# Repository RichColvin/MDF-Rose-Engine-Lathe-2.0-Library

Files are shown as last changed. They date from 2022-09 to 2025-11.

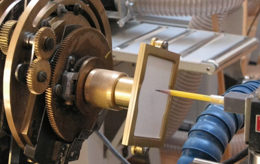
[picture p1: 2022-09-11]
NextionPreV22/Images/PaperChuck.png

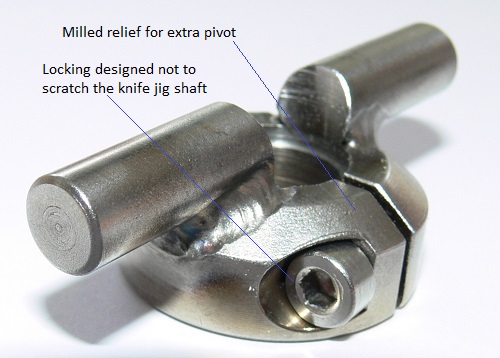
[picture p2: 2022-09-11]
Documents/MASTER - Documents/Images/Desktop/Tormek Add-on Parts/pivot_collar_3.JPG

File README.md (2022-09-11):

# MDF Rose Engine Lathe 2.0 Library
Code and images used for the MDF Rose Engine Lathe 2.0 Library web site (https://mdfre2.colvintools.com/)

This work is licensed under a Creative Commons Attribution-ShareAlike 4.0 International License.

To the extent that material may appear to be infringed, I assert that such alleged infringement is permissible under fair use principles in U.S. copyright laws. If you believe material has been used in an unauthorized manner, please contact me at the eMail listed above.

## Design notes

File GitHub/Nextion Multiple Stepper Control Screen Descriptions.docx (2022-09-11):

Nextion Multiple Stepper Control Screen Descriptions

V: 26r

Splash Screen

Purpose: Initialize program

Buttons explanation: Touching one of the top row buttons will take you to that screen. The ‘Load Ini’ button in the lower right corner will load motor settings from an ini file named 4Axes.ini. Restarting the program may be necessary for all the settings to be active.

4-Axes Driver Board

# Main Screen

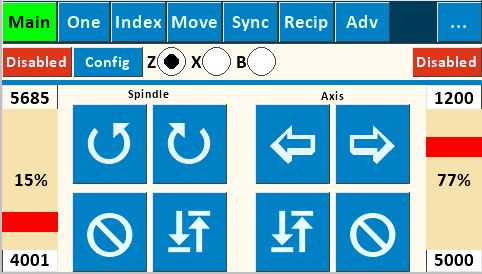
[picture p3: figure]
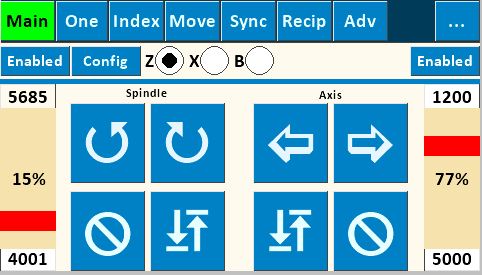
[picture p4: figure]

Purpose: Allows direct control of spindle speed and direction and auxiliary axis speed and direction independent of one another. Typically used for continuous spindle and/or continuous Axis motion (turning or facing cuts, continuous rose engine patterns on cylindrical or face surfaces., etc.).

Buttons explanation:

- “” (Counterclockwise) and “” (Clockwise) rotational arrows indicate direction of the Spindle. “”(In) and “”(Out) indicates direction of the selected axis. Rotation/movement continues until “” (Stop) is pushed.
- Right and left speed bars (for Spindle and Axes, respectively, are shown as a percentage of maximum speeds set on the Configuration Screen for “Main” and “Z, X, or B Axes”, respectively. Max speed and acceleration entry fields are shown at the top and bottom of each speed bar. These fields may also be set using the Configuration screen.
- “ “(Return): Returns the spindle or the selected axis to the start point of the previous operation.

# Number Pad Screen

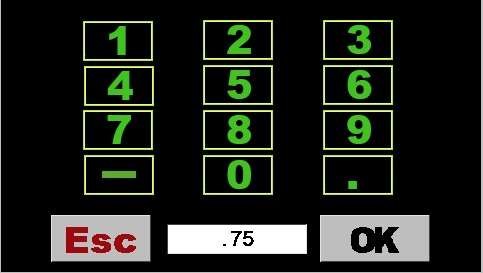
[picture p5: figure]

Purpose: This screen appears whenever any numerical value on any screen is tapped. Revise the number in the box by tapping the box multiple times to “backspace” over each digit or decimal point, and then re-enter the new value using the number pad buttons. Pressing “OK” saves the number back to the value box on the previous screen and returns user to that screen.

# Synchronization Screen

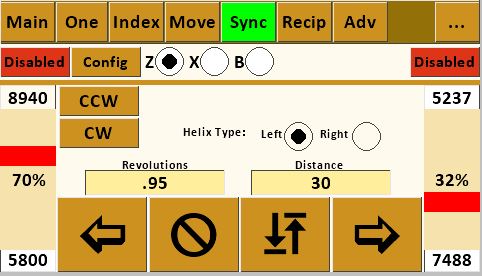
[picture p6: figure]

Purpose: Synchronizes the Spindle and Auxiliary Axis to produce helical patterns or threads on cylindrical surface of workpiece or to produce spirals on a face surface.

Buttons explanation:

- “Left” and “Right” determine whether helix runs clockwise or counterclockwise on the piece.
- “CW” (Clockwise) and “CCW” (Counterclockwise) index the spindle for the next cut path – either clockwise or counterclockwise per user design. Amount the spindle will index uses the value in “Size” set in the box on the Index #1 Screen (this value could be either in divisions of a circle or degrees depending upon which option is toggled on Index #1 Screen).
- “Revolutions” variable value determines how far around the piece the helix will travel based on the spindle rotating. The value of .5 illustrated will rotate spindle 360x.5=180 degrees.
- “Distance” variable value determines the cut length (amount of Z axis movement) and is dependent upon value entered in Setup Screen for “Distance/360”.
- Right and left speed bars (for Spindle and Axis, respectively, are shown as a percentage of maximum speeds set on the Configuration Screen for “Sync” and “Z Axis”, respectively. Note that slowest value on speed bars will “control” the other value.
- “”(In) and “”(Out) determine whether cut is made toward or away from headstock. Pattern will run the pre-determined “Distance” and then stop and wait for return direction instruction. User chooses whether to cut in both directions or retract cutter and return to start without cutting.
- “ “(Return): Returns both the spindle and the axis to the start point of the previous operation.
- See appendix for procedure for using the Synchronization Screen for thread cutting.

# Reciprocation – Axis Screen (Axial)

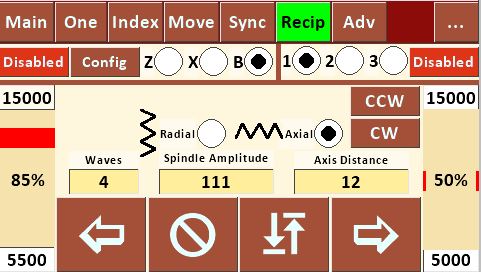
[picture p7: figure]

Purpose: Synchronizes Spindle and Auxiliary Axis to produce a reciprocating pattern along the longitudinal cylindrical surface of workpiece: It works by reversing spindle direction alternately while Z or X axis continues in the same direction.

Buttons explanation

- “1” Pattern is an equal angle on the up and down legs.
- “2” Pattern is a square wave.
- “3” Pattern is a like a sawtooth. The up leg is angled, the down leg is straight down.
- “CW” (Clockwise) and “CCW” (Counterclockwise) index the spindle for the next reciprocating cut path – either clockwise or counterclockwise per user design or desire. Amount the spindle will index uses the value set in the “Size” box on the Index #1 Screen (this value could be either in divisions of a circle or degrees depending upon which option is toggled on Index #1 Screen).
- “Wave Count” variable sets number of individual waves /\ to be cut along the cylinder.
- “Spindle Amplitude” variable sets “height” of each wave in degrees of rotation.
- “Axis Distance” variable determines the cut length for entire pattern (amount of Z, X, or B axis movement) and is dependent upon value entered in Setup Screen for “Distance/360”.
- “”(In) and “”(Out) determine whether cut is made toward or away from headstock. Note that “”(In) starts with a downward move and “”(Out) starts with an upward move (test your individual machine and apparatus to verify – your results may vary). Pattern will run the pre-determined “Axis Distance” and then stop and wait for return direction instruction. User chooses whether to cut in both directions or retract cutter and return to start without cutting.
- “ “(Return): Returns both the spindle and the axis to the start point of the previous operation.

# Reciprocation – Spindle Screen (Radial)

Purpose: Synchronizes Spindle and Auxiliary Axis to produce a sharp-pointed reciprocating pattern along the circumferential surface of a cylindrical workpiece: It works by alternately reversing Z or X axis direction while spindle continues rotating in the same direction.

Buttons explanation

- To navigate to this screen, start with “Rec” and toggle from Axial to Radial.
- “1” Pattern is an equal angle on the up and down legs.
- “2” Pattern is a square wave.
- “3” Pattern is a like a sawtooth. The up leg is angled, the down leg is straight down.
- Small “”(In) and “”(Out) move the Z or X axis to the next pattern starting position. Z or X axis movement will be the value of “Distance” set on the Move Screen for that axis.
- “Return” button rotates the spindle to the pattern start point.
- “Acceleration” and “Speed” values for this screen are set here for both Spindle, Z, and X axes. See notes on value limitations under Configuration Screen explanation. Because of synchronization of the spindle and Z or X axis speeds, one of the maximum speeds will control the other.
- “Wave Count” variable sets number of individual waves ( > ) to be cut along the cylinder.
- “Spindle Degrees” variable sets the circumferential distance around the cylinder for the total pattern. Entering 360 would wrap the pattern all the way around the cylinder; entering 90 would condense the whole pattern around just 90 degrees of the cylinder.
- “Axis Amplitude” variable sets “height” (distance along Z, X, or B axis) of each wave and is dependent upon value entered in Setup Screen for “Distance/360”.
- Large “”(In) and “”(Out) buttons determine the direction of cut around the spindle. Pattern will run the pre-determined “Spindle Degrees” then stop and wait for return direction instruction. User chooses whether to cut in both directions (either on the same cut path or on subsequent path) or retract cutter and return to the origin point without cutting.
- “ “(Return): Returns both the spindle and the axis to the start point of the previous operation.

# One Screen (Single Stepper Screen)

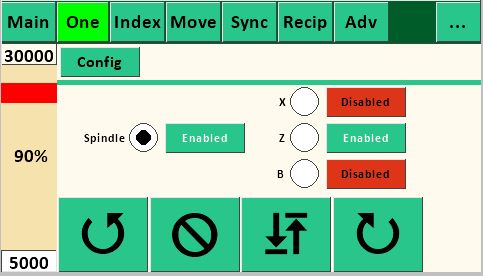
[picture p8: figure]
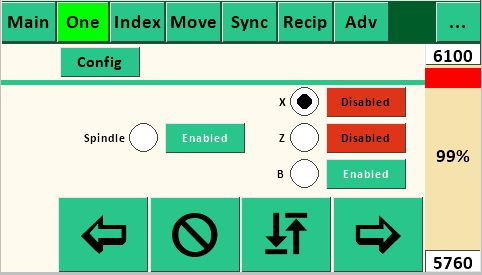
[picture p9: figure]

Purpose: Allows control of either the spindle or a single axis speed and direction. Useful for secondary spindle operation such as higher or lower speed functions than the Main Screen.

Buttons explanation

- “Enabled” shows status (either “Enabled” or “Disabled”) of either Spindle stepper motor or an Axis stepper motor as selected. If enabled, the motor is in locked status; if disabled, the selected motor can be repositioned. Default is “Disabled”. Primary use for these buttons is to lock the spindle or axis while performing another operation.
- “” (Counterclockwise) and “” (Clockwise) rotational arrows indicate direction of the Spindle .“”(In) and “”(Out) buttons indicate direction of an axis. Movement continues until “Stop” is pushed.
- Speed bar is shown only for the selected axis or spindle.

# Index Screen

Purpose: Allows indexing spindle for use in index work or other uses.

Buttons explanation

- 1-5: Individual indexes
- “Div” radio button sets the indexing to number of divisions of a full rotation, toggling to “Deg” sets the indexing to number of degrees.
- “Index” box shows current completed index
- “Next Index” shows ID of the next index. It will show lower ID if the CW button was last touched and higher if CCW button was touched
- Speed bar is shown as a percentage of maximum speeds set on the Configuration Screen for “Index”.
- “Divisions” of a circle or “Degrees”, depending upon which is toggled. Note that the value of the selected index (1 through 5) is used by the “CW” and “CCW” indexing movements on the Synchronization Screen and the Reciprocation – Axis Screen in either “Divisions” or “Degrees”, depending upon which is toggled.

# Index #2 Screen with file dropdown open

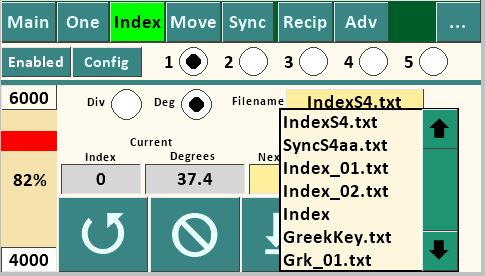
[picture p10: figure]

Purpose: Allows variable index sizes to be retrieved sequentially from a file stored on a microSD card. This feature could be used to place evenly spaced features (such as barleycorns) around the circumference of an ellipse (i.e. equal division of the ellipse), with the angular movement in degrees precalculated using a CAD program.

Selecting the filename text box will open a dropdown list of files located on the microSD card. Use the Up and Down arrows to traverse the file list. While the dropdown list is active, all other controls on the page are disabled. The dropdown list can be closed either by selecting a file, or by touching the Filename textbox. Each Index may have its own file.

The file format is ASCII text (numbers, letters, and decimal only) with each number on a new line, saved to the microSD card using a separate computer. Because the SD Card library only supports the 8.3 or Short File

Name convention, the file name must be a maximum 8 characters + a period + three-character extension (thus the 8.3); the name is not case sensitive. It's not necessary to have the extension, but the limit for the name is 8 characters when no extension is used. Multiple files can be loaded onto the microSD card for use on one or more work pieces as desired.

The counterclockwise and clockwise arrows determine direction of spindle movement during indexing. When using the “File” version, each successive index will read successive file numbers off the microSD card (in either “Div” or “Deg” as selected on this screen). When the end of the file is reached, “Size” will be reset to 0. The “Index” value will be increased when indexing clockwise and decreased when indexing counterclockwise. The read position of the file can also be set by editing the “Index” value.

The “Div” and “Deg” radio buttons and the “Enabled” button work the same as on the other Index screens above.

# Move Screen

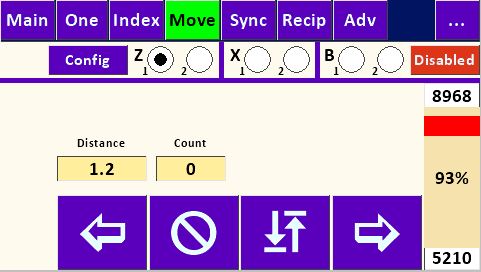
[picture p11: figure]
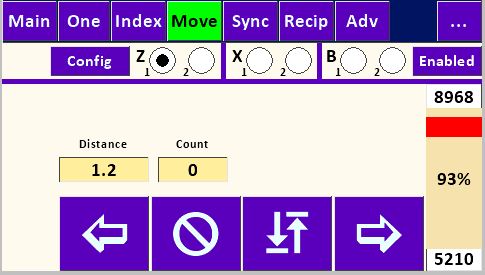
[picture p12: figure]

Purpose: Moves the Z or X Axis a specific distance and direction. This could be used to cut a flute or other element along Z Axis of specific length, or used on the end face of a cylinder if set up to drive the X Axis, to move a specific distance to produce rose engine basket weave or other repeating design element on the cylindrical surface of the workpiece, or to plunge in and out of cylindrical surface to do index work if set up for X Axis. Each axis has two separate move settings.

Buttons explanation:

- “Distance” variable sets amount of movement along Z or X Axis and is controlled by Setup Screen Value “Distance/360”.
- “Count” tracks the number of moves.
- “Total” tracks total distance of movement (adding in one direction, subtracting in the other.
- “In” and “Out” indicate direction of the Axis movement. Movement will continue for “Distance” set and then stop and wait for another move instruction, either repeating move or returning to origin.
- Speed bar is shown as a percentage of maximum speed set on the Configuration Screen for “Z or X

Axis”.

Advanced Screen

The Advanced screen contains links to three other pages, Rose, Greek Key, and Program.

# Rose Screen

Purpose: Create Rose or single stage geometric chuck patterns, see Wikipedia Rose (mathematics) (https://en.wikipedia.org/wiki/Rose_(mathematics)).

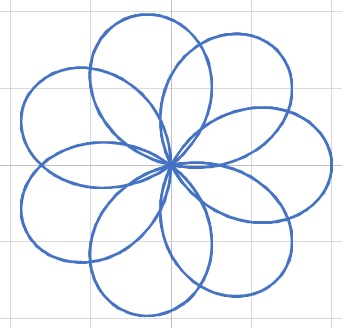
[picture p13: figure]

Buttons explanation:

- “n” numerator.
- “d” denominator.
- “k” ratio of n/d.
- “Amplitude” variable sets “height” (distance along Z or X Axes) of each lobe and is dependent upon value entered in Setup Screen for “Distance/360”.
- “” (Clockwise) and “” (Counterclockwise) rotational arrows indicate direction of the Spindle. Rose pattern continues until “Stop” is pushed.
- “ “(Return): Returns both the spindle and the axis to the start point of the rose pattern.
- Note: B axis is only available when it is set to Linear on the B Axis Configuration page.

# Grk (Greek Key) Pattern Screen

Purpose: Create Greek Key or Meander patterns. The Pattern page has six built-in patterns. Patterns are created by moving either the spindle or one of the axes individually.

Buttons explanation:

- Pattern: Create a Greek Key using one of the built-in patterns.
- File: Create a Greek Key by reading values from a file. See below.
- Radial or Axial: Creates a pattern radially (circumferentially) of axial.
- 4a and 4b: Create a pattern four segments wide. 4a is eight segments tall, 4b is thirteen segments tall.
- 3a and 3b: Create a pattern three segments wide. 3a is four segments tall. 3b is eight segments tall.
- 2a and 2b: Create a pattern two segments wide. 2a is three segments tall. 2b is six segments tall.
- Length: Specifies the length of the shortest Z or X axis segment. Each pattern will have segments which are a multiple of the shortest segment.
- Patterns Per 360: Specifies how many individual patterns will fit in 360 degree rotation of the spindle. This controls the length of the shortest spindle segment.
- Count: Determines the actual number of patterns to create. Setting it less than the Patterns Per 360 value will leave a space at the end of the pattern. Setting it larger will recut the same pattern. This is useful when you want to cut a pattern deeper. Grey box shows the current executing pattern count.

The following shows each pattern. The numbers by each segment indicate the length of that segment. The arrows show the direction the cutter is traveling. When the arrows change color it indicates the next segment’s direction.

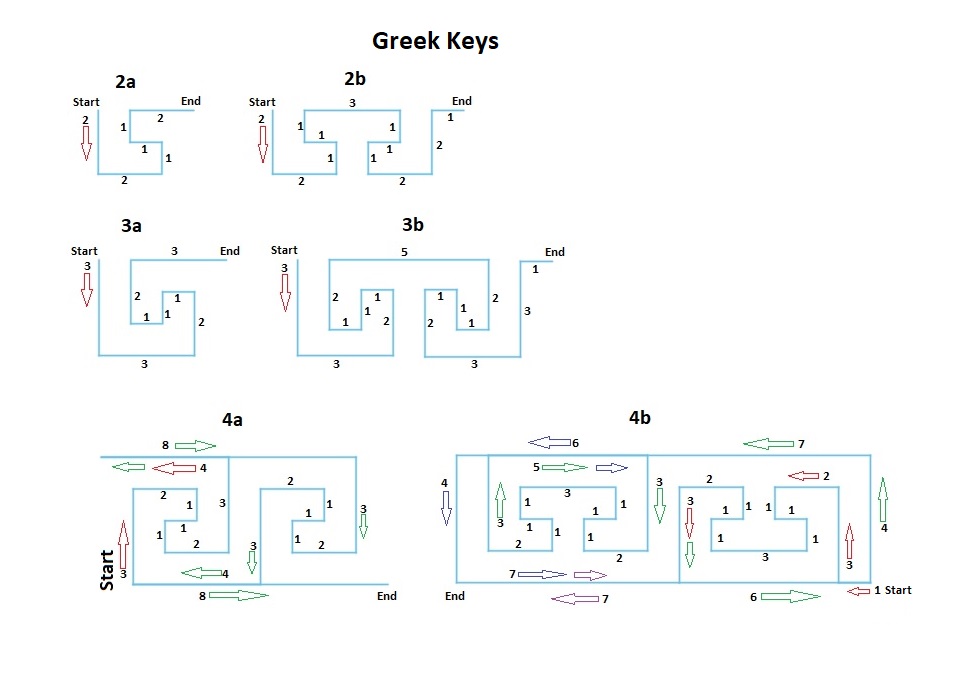
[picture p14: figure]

# Program from File Screen

Purpose: Create Greek Key or Meander patterns by reading values from a file.

Buttons explanation:

- Filename must be in 8.3 format: 8 character name, a period, and a 3 character extension. It isn’t necessary to have the full 8.3 characters. Note: Apple computers may automatically add “.txt” to the name.
- Selecting the filename text box will open a dropdown list of files located on the microSD card. Use the Up and Down arrows to traverse the file list. While the dropdown list is active, all other controls on the page are disabled. The dropdown list can be closed either by selecting a file, or by touching the Filename textbox.
- Segments: Values in the file are interpreted as a multiplier of the “Length” for the Z, X, and B axes and as a multiplier of the calculated segment size for the spindle. Floating point numbers are valid.
- Actual: Values in the file are used as the length of the move. Floating point numbers are valid.
- Grey boxes: Command, Segments, and Line# show the values for the current line in the file being executed. Count shows the current executing pattern count.

File format:

The file must be plain text (ASCII).

Each line in the file must begin with an axis identifier letter and end with the length of the move, except for the Comment and End lines.

Identifiers:

- ; Comment: Begins with a semi-colon, “;”, and may have up to 25 characters. There is no limit on the number of comment lines in a file. Each comment line must have a least one additional character.
- E End: Begins with a capital “E”. All files must have this as the last line in the file.
- WS(Plus count of vertical segments in the pattern). Required for all radial patterns.
- WA(Plus count of horizontal segments in the pattern). Required for all axial patterns.

The following commands can be interpreted as having a multiplier or as the actual size of the move.

- A(Plus multiplier or actual length) Negative number moves axis towards the spindle, positive moves away.
- S(Plus multiplier or actual length) Negative number moves spindle CCW, positive moves CW.
- H(Plus multiplier or actual length)V(Plus multiplier or actual length) Specifies a coordinated diagonal move with the spindle and the active axis. H is a horizontal move with the axis and V is vertical move with the spindle. Each move is a leg of a right triangle.
- P(Plus multiplier) Pause in seconds.
- O(Plus multiplier or actual length) Moves the cutter away from the workpiece.
- I(Plus multiplier or actual length) Moves the cutter into the workpiece.
- X(Plus multiplier or actual length) Moves X axis. Negative numbers reverse direction.
- Z(Plus multiplier or actual length) Moves Z axis. Negative numbers reverse direction.
- B(Plus multiplier or actual length) Moves B axis. Negative numbers reverse direction.
- C(Plus multiplier or actual length) Moves Spindle. Negative numbers reverse direction. (C is a rotary axis parallel to the spindle and to Z.)

Page commands. These use settings on the individual pages

- ~~Q~~~~M(Plus multiplier) Moves an axis using settings on the MOV page. -1 multiplier moves towards the headstock, 1 moves away from the headstock.~~
- ~~QI~~~~(Plus multiplier) Index the spindle using settings on the IND page. -1 multiplier moves CCW, 1 moves CW.~~
- ~~QR~~~~(Plus multiplier) Reciprocate using settings on the REC page. -1 multiplier moves towards the headstock, 1 moves away from the headstock.~~
- ~~QS~~~~(Plus multiplier) Synchronize spindle and axis using settings on the SYNC page. -1 multiplier moves towards the headstock, 1 moves away from the headstock.~~

Page settings. These set parameters on the pages.

Sync page:

- GG(Plus multiplier) Synchronize spindle and axis using settings on the SYNC page. -1 multiplier moves towards the headstock, 1 moves away from the headstock.
- GH - Sync Helix Type 0=left 1=right
- GD - Sync Distance (floating point)
- GR - Sync Revolutions (floating point)

Recip page:

- VV(Plus multiplier) Reciprocate using settings on the RECIP page. -1 multiplier moves towards the headstock, 1 moves away from the headstock.VT - Recip Radial =0 Axial=1
- VK - Recip Style
- VW- Recip Waves (Integer)
- VS - RecipSpindle (floating point)
- VA - Recip Axis (floating point)

Move page:

- FF(Plus multiplier) Moves an axis using settings on the MOVE page. -1 multiplier moves towards the headstock, 1 moves away from the headstock.
- FD - Move Distance (floating point)

Index page:

- NN(Plus multiplier) Index the spindle using settings on the INDEX page. -1 multiplier moves CCW, 1 moves CW.
- NT - Index Divisions=1 Degrees=2
- ~~NI - Index Division or degrees size (floating point)~~
- ND- Index Division or Degrees size (floating point)
- NJ - Index ID (Integer from 1 to 5)

M3 Parameters

- JR – M3 radius (floating point)

Enable/Disable Steppers

- KS(Plus multiplier) Enable or Disable Spindle. Disable = 0, Enable =1.
- KX(Plus multiplier) Enable or Disable X Axis. Disable = 0, Enable =1.
- KZ(Plus multiplier) Enable or Disable Z Axis. Disable = 0, Enable =1.
- KB(Plus multiplier) Enable or Disable B Axis. Disable = 0, Enable =1.
- KA(Plus multiplier) Enable or Disable current Program page axis. Disable = 0, Enable =1.
- Note: Steppers are automatically enabled when executing a command, so it is not necessary to enable one after disabling it.

Example file:

;Pattern 2a
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
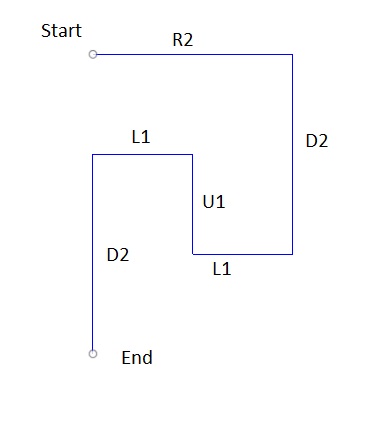
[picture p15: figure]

# Configuration Screens

Purpose: The factors on these screens control how speeds and distances are determined. The left columns show settings on the Nextion. Touching one of the text boxes allows you to edit that value. The right columns show settings stored on the Teensy. These are read only and should match the left column settings.

# Spindle

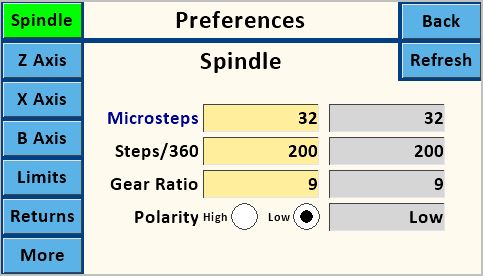
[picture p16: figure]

Buttons explanation:

- The software is currently set up for 32 Microsteps, 200 Steps/360, and 9 Gear Ratio for the spindle. This assumes a stepper motor with 200 steps per revolution and is the “standard” configuration for the

MDF Rose Engine with a 12 tooth spindle motor drive pulley and 108 tooth driven pulley yielding a Gear Ratio of 9. Once set, the values for the Spindle will remain the same unless changes are made to spindle drive setup.

Z Axis

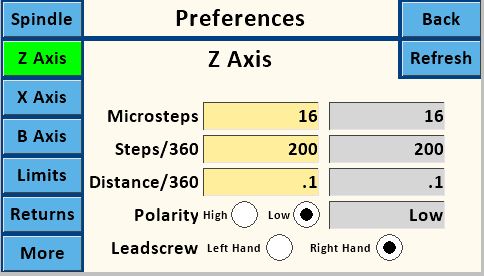
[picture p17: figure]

- The Z axis screen shows 16 Microsteps, and that you are using a stepper motor with 200 Steps/360. This is intended to show microstep values must use valid values for the stepper driver, usually 1, 2, 4, 16, 32, 64, and 128. These settings must match the jumper settings on the PCB.
- The B Axis can be configured as either a radial axis, like a spherical apparatus or a spindle, or as a linear axis. The B axis on the Main and One screens only uses speed settings. When configured as a radial axis for a spherical device it uses a calculated distance along the circumference based on the radius length between the spherical device pivot point and the cutter. The ‘B Radius’ text box will appear on a page when the B axis is active and the B axis is set to Radial.
- The “Distance/360” is the distance the Z axis carriage moves in one revolution of its stepper motor. It is a value arrived at empirically by measuring the movement of the Z Axis using a dial indicator or other appropriate device while the stepper motor revolves a set number of turns. This can be accomplished by entering a value in “Distance/360” such as 1, then using the Move Screen to move a “Distance” of 20 while measuring. This should turn the motor through 20 full revolutions. Divide the distance traveled by 20 and enter calculated value into “Distance/360”. If the total distance moved in 20 revolutions is insignificant, use a larger “Distance” number like 50 (or even 100). Note that best practice is to remove backlash from the Axis mechanism prior to the measurement run by moving the axis in the same direction. It may be possible to get a starting point for Distance/360 by calculation calculating the stepper pulley to driven pulley ratio, and/or the thread pitch.

Finally, it’s important to note that if you use different pieces of apparatus (such as a cross-slide, a spherical or a curvilinear apparatus) with the Z Axis, each will likely have a different value for Distance/360, so keep track of these separately for each piece of apparatus.

- The Enable “High” and “Low” radio buttons for both Spindle and Z Axis are set to “Low” by default, which is the correct setting when using the DRV8825 Stepper Drivers. The “High” setting is for use for some external stepper drivers.
- “Hand” should be set to the thread direction of the axis leadscrew. If using a Hardinge compound sliderest with a left-hand thread, for example, set “Hand” to “L”. If using an apparatus with a righthand threaded rod, for example, set “Hand” to “R”. Test to verify.
- “Back” button returns to the previous screen.
- “Limits” button activates the Limits Screen.
- “Returns” button activates the Returns Screen.
- “Refresh”: Retrieves settings stored on the Teensy. These settings should match the left columns which are stored on the Nextion.

X Axis

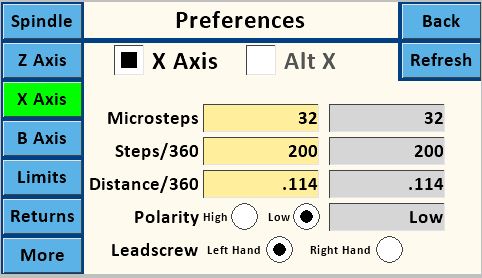
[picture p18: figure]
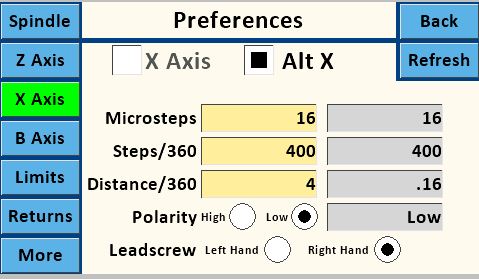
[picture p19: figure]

- The X axis can use two different steppers. Alternate X will usually be used to adjust a curvilinear arm while the main X axis is floating.

B Axis

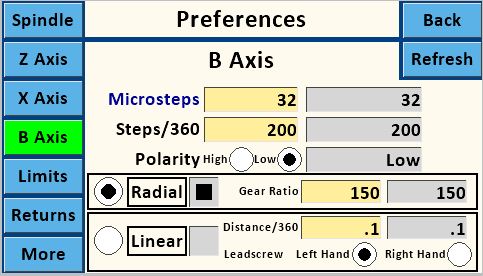
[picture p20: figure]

- The B Axis may be used as a radial axis, for example with a spherical apparatus, or as a linear axis.

Limits screen

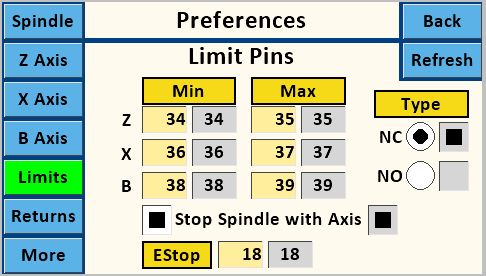
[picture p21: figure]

Purpose: Set pin numbers for limit switches.

Limit switches and Estop switch(s) can be wired either normally closed or normally open. Normally closed is recommended. Multiple switches may be wired together serially, not parallel.

When a limit switch is triggered, the action button for that direction limit switch will turn red. No further action can be taken until the “” (Stop) button is touched. Once that is done, the opposite direction action button can be touched while the limit switch is still closed.

Limit Max triggered:

Limit Min triggered:

When EStop switch is triggered, the action buttons will turn red. No further action can be taken until one of the “” (Stop) buttons is touched and the EStop switch is not closed.

Returns screen

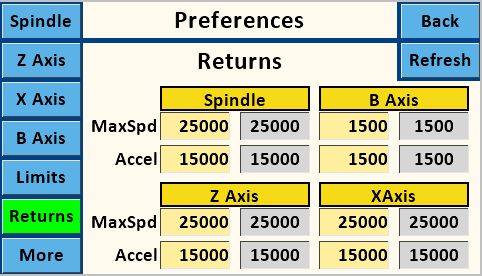
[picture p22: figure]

Purpose: Set speed and acceleration for return actions.

# Config Screen

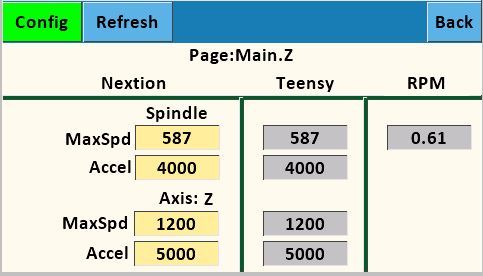
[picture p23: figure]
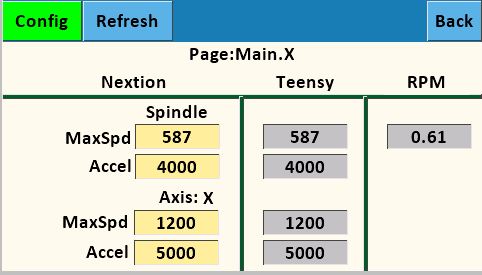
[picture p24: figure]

Purpose: Set speeds and acceleration values for all other screens with speed bars. Values shown are for the previously active screen. Each of the functional screens have unique settings for all variables. The left column shows settings on the Nextion. Touching one of the text boxes allows you to edit that value. The right column shows settings stored on the Teensy. These are read only and should match the left column settings.

Buttons explanation:

- Set “MaxSpd” and “Accel” values for each of the screens listed. The upper rows control the lathe spindle in each screen, the lower rows control the Axis. Note that if you use different pieces of apparatus (such as a cross-slide, a spherical or a curvilinear apparatus, etc.) with the Z Axis settings, it will probably be desirable to reset the MaxSpd for some uses. Keep a record of different settings used for each piece of apparatus. Generally speaking, the “MaxSpd” settings can be set anywhere between 100 and 50000 with 10000 being a safe starting point. Acceleration can be set between 100 and 500000 with 1000 being a good starting point.
- “Show Config” runs a routine to return the current settings stored on the Teensy. Settings are also stored on the Nextion and can be out of sync when new software is loaded on either the Teensy or the Nextion. Running “Show Config” should be done each time new software is loaded into either the Teensy or the Nextion.
- “Back” button returns to the previous screen.
- RPM grey box shows the calculated RPM of the spindle.
- Preliminary testing by the prototyping group for initial settings (assuming a 2” diameter workpiece) resulted in the following recommendations:
  - For roughing out a cylindrical workpiece (planing cut) using Main Screen (use 100% on speed bars), set MaxSpd on Sync to 5000, Accel to 500.
  - For finish cut, lower the Axis speed bar to usable speed for smooth cut.
  - For Helical cut along cylinder using Sync Screen, set MaxSpd for Sync to 250, MaxSpd on Z Axis to 500.

More screen

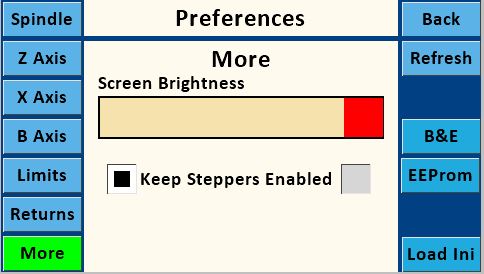
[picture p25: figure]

Screen Brightness slider will change the brightness of the screen.

The ‘Show BE’ button will show the BE icon in the other pages’ toolbars. Clicking on the icon will toggle visibility of the icon on and off.

‘EEPROM’ button shows the values stored in EEPROM on both the Nextion and Teensy. It is used to verify the settings match. Mismatches can occur when updating the software.

The ‘Load Ini’ button will load motor settings from an ini file. Restarting the program may be necessary for the settings to be active. While Load Ini is running, the Key, Setting, and Value fields will show the current values being updated.

EEPROM screen

Column 1 lists all of the settings for a page. Column 2 shows current settings on the Nextion. Column 3 shows the settings on the Teensy.

B&E screen

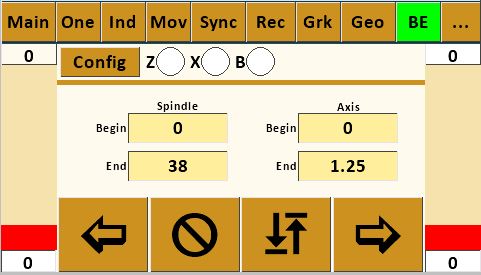
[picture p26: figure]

Currently under development. Only the Begin and End text boxes are active. They show the distance or degrees an axis or the spindle has moved from the start of the last operation on another screen. This can be used to verify the specified movement matches the actual movement.

# Appendix

General Notes:

1. When first setting up or when updating Teensy or Nextion software, go to each screen in turn and refresh all settings by entering new or current values in the text boxes and pressing “OK”, cycling the radio buttons, and moving the speed sliders.
2. X, Z, and B axes for the lathe in descriptions above use the standard shown here:

# Exercises

I. Thread Cutting for Boxes with the Synchronization Screen:

Note: refer to instructions in other resources (such as “Turning Threaded Boxes” by John Swanson, Schiffer Publishing, 1999) for box threading tips and techniques.

Example 1: Single-start thread of 16 threads per inch (1/16” pitch).

1. Set “Revolutions” to number of threads to be cut around the cylinder. Suggest using “4” as a starting point.
2. Set “Distance” to .25 (four threads at 1/16” = ¼”).
3. With a 60-degree double angle cutter running in a drilling frame set parallel to the lathe’s spindle and driven by the overhead, test and adjust Spindle and Axis speed bars as necessary to get a usable combination of feed and speed (not so fast as to bog down cutter, not so slow as to burn the wood). If necessary, adjust “MaxSpd” setting on Configuration Screen to get usable combination.
4. Test “Left” and “Right” radio buttons to determine which type of thread will be cut (left hand or right hand).
5. Choose whether to cut “In” or “Out” based on what makes sense for your piece.
6. Cut thread. Typical good practice uses roughing and final cuts for each thread. If wood tends to fuzz up or chip out, it’s common practice to flow some CA glue into the rough threads and let it cure prior to the final cut.

Example 2: Four-start thread of 16 threads per inch (1/16” pitch, ¼” lead)

1. Set “Revolutions” to number of threads (of each start) to be cut around the cylinder. Suggest using “1” as a starting point.
2. Set “Distance” to .25 (1/4” lead). This will cut one continuous thread traveling ¼” as it goes once around cylinder.
3. Got to Index #1 Screen. Select “Div” toggle and set value in “Size” box to “4”. Note: would also work to select “Deg” toggle and set value in “Size” box to “90”.
4. Follow steps 3, 4, 5 & 6 in Example 1 above.
5. Return to starting point with cutter retracted from work using “In” or “Out” as appropriate.
6. Index spindle using either CW or CCW based on personal preference to get to starting point of next thread start. Re-engage cutter and repeat cutting process(es) in step 6 in Example 1 for Start #2. Retract cutter and return to start point of Start #2.
7. Repeat indexing and cutting procedures for Starts #3 and #4.

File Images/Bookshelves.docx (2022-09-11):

MDF Rose Engine Lathe 2.0

MDF Rose Engine Lathe 2.0

MDF Rose Engine Lathe 2.0

User's Guide Nextion Multiple Stepper Control
| Best Practices | Cleaning, Lubrication, and Other Maintenance | Sharpening Rose Engine Fly Cutters

MDF Rose Engine Lathe 2.0

MDF Rose Engine Lathe 2.0

MDF Rose Engine Lathe 2.0

MDF Rose Engine Lathe 2.0

MDF Rose Engine Lathe 2.0

Ver 1.1, 10 Dec 20

Ver 1.0, 01 Dec 20

| | Design Goals Ver 1.0 11 Aug 20 MDF Rose Engine Lathe 2.0 | Standards | Instructions for Building Base and Headstock | Instructions for Building Stepper Controls System | Upgrading the Stepper Controls System
What Changed? | Frequently Asked Questions MDF Rose Engine Lathe 2.0

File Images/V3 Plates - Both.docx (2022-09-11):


Teensy MicroSD Card

HMI Display

Stepper Motors

Spindle

X

M4

M3/B

Z

Limit Switches

37

Stop (34)

Max (39)

Min (38)

Overhead Drive

Reset

Power Indicator

Power

Main Power

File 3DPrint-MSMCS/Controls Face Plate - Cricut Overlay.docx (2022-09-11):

Power

HMI

Quick

Stop

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
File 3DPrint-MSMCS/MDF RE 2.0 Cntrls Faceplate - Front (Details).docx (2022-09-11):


Memory Card

Display

Spindle

M3 / B

M4

X

Z

E-stop

Other

Max

Min

Limit Switches

Overhead Drive On

Overhead Drive Reset

Overhead Drive Power

Main Power

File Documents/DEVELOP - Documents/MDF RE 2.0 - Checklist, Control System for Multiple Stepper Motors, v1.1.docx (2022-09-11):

Control System for Multiple Stepper Motors

Setup and System Checkout

System For
Checked by
Date

1 | System Load | ✓
1.1 | Load Teensy program Teensy Model Software Version Loaded
1.2 | Load Nextion configuration Nextion Model Software Version Loaded
1.3 | Load Teensy INI file Preferences Shared Limits Sync Returns Recip Main GreekKey Multi Program Index Rose Move

2 | Main Function | ✓
| Spindle
2.1 | Rotation
| Z Axis
2.2 | Move
| X Axis
2.3 | X axis - move
| M3 Axis
2.4 | Linear movement
2.5 | Rotation
| M4 Axis
2.6 | Linear movement
2.7 | Rotation

3 | One Function | ✓
| Spindle
3.1 | Rotation
| Z Axis
3.2 | Move
| X Axis
3.3 | X axis - move
| M3 Axis
3.4 | Linear movement
3.5 | Rotation
| M4 Axis
3.6 | Linear movement
3.7 | Rotation

4 | Index Function | ✓
| Spindle
4.1 | Index by Divisions – 4
4.2 | Index by Divisions – 8
| M3 Axis
4.3 | Index by Divisions – 4
4.4 | Index by Divisions – 8
| M4 Axis
4.5 | Index by Divisions – 4
4.6 | Index by Divisions – 8

5 | Move Function | ✓
| Z Axis
5.1 | Linear movement
| X Axis
5.2 | Linear movement
| M3 Axis
5.3 | Linear movement
5.4 | Rotation
| M4 Axis
5.5 | Linear movement
5.6 | Rotation

6 | Sync Function | ✓
| Z Axis
6.1 | Helix type Left | CCW
6.2 | Helix type Right | CCW
6.3 | Helix type Left | CW
| X Axis
6.4 | Helix type Left | CCW
6.5 | Helix type Right | CCW
| M3 Axis
6.6 | Helix type Left | CCW
6.7 | Helix type Right | CCW
| M4 Axis
6.8 | Helix type Left | CCW
6.9 | Helix type Right | CCW

7 | Recip Function | ✓
| Z Axis / Radial
7.1 | Pattern 1 | CCW
7.2 | Pattern 2 | CCW
7.3 | Pattern 3 | CCW
7.4 | Pattern 1 | CW
| Z Axis / Axial
7.5 | Pattern 1 | CCW
7.6 | Axial | Pattern 2 | CCW
7.7 | Axial | Pattern 3 | CCW
| X Axis / Radial
7.8 | X axis | Radial | Pattern 1 | CCW

8 | Greek Key Function | ✓
| Radial
8.1 | 2a pattern
8.2 | 2b pattern
| Axial
8.3 | 2a pattern

9 | Limit & Stop Switches | | | ✓
9.1 | Limit Switch | Pin #
9.2 | Limit Switch | Pin #
9.3 | Limit Switch | Pin #
9.4 | Stop Switch | Pin #

Comments:

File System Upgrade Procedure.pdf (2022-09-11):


### Step 1 – Get a copy of the Teensy program file

Download 4Rose.hex to your computer.

### Step 2 – Get a copy of the Nextion configuration file

Download RoseEngine_14.tft, and put it in the root folder of a microSD card.

Notes:
1. You can only have one file on this card which is a .TFT file. The upgrade will not work if there is a 2d one.
2. You need to check for hidden
files on the microSD card. I
found that hard to do on


macOS (which created a hidden TFT file) and had to do this on a Raspberry Pi.

### Step 3 – Get a copy of the 4Axes.ini settings file

Download 4Axes.ini, and put it in the root of a second microSD card

### Step 4 - Upgrade the Teensy

Step 4a
Connect the computer to the Teensy.


- The cable end connected to the Teensy uses a MicroUSB connector.
- The Teensy’s jack is noted in the picture to the right.

Notes:
1. Be sure you have a good MicroUSB cable. Some are only used for charging a device (and they are usually longer). These will often not work.

Step 4b

On the Computer, start the Teensy Loader. The icon looks like the one to the right.

Note:
1. If you don’t have the Teensy Loader, you can get it from https://www.pjrc.com/teensy/loader.html.
Step 4c

Be sure the system shows that the Teensy is connected. This is evident when the Auto button is illuminated green. As noted in step 4a above, if your USB cable is bad, this won’t light.

The default for the CPU selected won’t handle the whole 4Rose.hex file, so if you try to open it, you will get the message as shown here.

Step 4d

Press the button on the Teensy to load the get the Teensy loader to recognize which CPU you are using.

Step 4e

Back on the Computer, using the Teensy Loader, open 4Rose.hex.

Once this is loaded, the bottom message will change to reflect the file size. (this picture was not updated).

Step 4f

Press the button on the Teensy to load the program file.

Disconnect the computer from the Teensy, and then reboot the Teensy.

### Step 5 – Upgrade the Nextion

Secure the microSD card which has the Nextion configuration file (from step 2).

Put this microSD card into the Nextion’s microSD card slot.

Reboot the Teensy again.

If this works as expected, it will read

Check Data … 100%
Updated Successed!

(guess that is a bad translation from
Chinese).


After that message appear, remove the microSD card from the Nextion, and reboot the Teensy again.

### Step 6 - Load the .ini file


Secure the microSD card which has the 4Axes.ini settings file
(from step 3).

Put this microSD card into the Teensy’s microSD card slot.

Start the system and click the Load ini button.

The Load ini button will turn green, and then it will
take off.

Once completed, a message will appear saying

Done – Restart may be needed.

Reboot the system one last time.

### Step 7 – Verify the Settings


It's a good practice to verify all of the settings once you've completed the steps.

1. Touch the Config button on each page and verify the Teensy column is populated with the same numbers as the Nextion column. Repeat for each axis on each page.
2. Next verify the Preferences are correct for the Spindle, Axes, Limits, and Returns.
3. Select the Main page, then the '...' (Preferences) page. Select the More page. Touch EEPROM. Repeat for each page and axis on the page. This will show all of the settings for the selected page.
A copy of the settings file (4Axes.ini) is on the following sheets.

### Config file settings

;==================================== [Setup]
;==================================== BoardType=4
Microsteps_Spindle=32
StepsPer360_Spindle=200
GearRatio_Spindle=9
Polarity_Spindle=1

;Z Axis
Microsteps_Z=32
StepsPer360_Z=200
DistancePer360_Z=.02
Polarity_Z=1

;X Axis
Microsteps_X=32
StepsPer360_X=200
DistancePer360_X=.02
Polarity_X=1

;B Axis
Microsteps_B=32
StepsPer360_B=200
GearRatio_B=150
Polarity_B=1
DistancePer360_B=1.02
RadialOrLineal=0
BRadius=5

;==================================== [Limits]
;==================================== ;Limit Switches
Min_Z=34
Max_Z=35
Min_X=36
Max_X=37
Min_B=38
Max_B=39

;==================================== [Returns]
;==================================== ;Return
MaxSpeed_Spindle=15011
Accel_Spindle=15012

MaxSpeed_Axis_Z=15013
Accel_Axis_Z=15014

MaxSpeed_Axis_X=15015
Accel_Axis_X=15016

MaxSpeed_Axis_B=15017
Accel_Axis_B=15018

;==================================== [Main]
;==================================== ;Axis Ids:
;-----------------
;Z=0
;X=1
;B=2
;Spindle=3

;-----------------
AxisId=0
;Spindle
MaxSpeed_Spindle=15000
Accel_Spindle=15001
SpeedPercentage_Spindle=30

;Z Axis
MaxSpeed_Z=4001
Accel_Z=5002
SpeedPercentage_Z=53

;X Axis
MaxSpeed_X=4000
Accel_X=5005
SpeedPercentage_X=10

;B Axis
MaxSpeed_B=5007
Accel_B=5008
SpeedPercentage_B=59

;==================================== [One]
;==================================== AxisId=3
;Spindle
MaxSpeed_Spindle=25060
Accel_Spindle=20061
SpeedPercentage_Spindle=61 ;Z Axis
MaxSpeed_Z=5062
Accel_Z=5063
SpeedPercentage_Z=64
;X Axis
MaxSpeed_X=5065
Accel_X=5066
SpeedPercentage_X=67
;B Axis
MaxSpeed_B=5068
Accel_B=5069
SpeedPercentage_B=70

;==================================== [Ind]
;==================================== IndexId=1
MaxSpeed_Spindle=5070
Accel_Spindle=5071
SpeedPercentage_Spindle=72 ;-----------------
;Division:0 Degrees:2
;Fixed:0 File:1
;-----------------
;Index 1
DivisionsOrDegrees_1=2
FixedOrFile_1=0
Size_1=1.875
;Index 2
DivisionsOrDegrees_2=2
FixedOrFile_2=0
Size_2=24.375
;Index 3
DivisionsOrDegrees_3=2
FixedOrFile_3=0
Size_3=90

;==================================== [Mov]
;==================================== AxisId=0
;Z Axis
MaxSpeed_Z=5080
Accel_Z=5081
SpeedPercentage_Z=82
Distance_Z=3

;X Axis
MaxSpeed_X=5083
Accel_X=5084
SpeedPercentage_X=85
Distance_X=5.75

;B Axis
MaxSpeed_B=5086
Accel_B=5087
SpeedPercentage_B=88
Distance_B=5.78

;==================================== [BE]
;==================================== AxisId=0
;Spindle
MaxSpeed_Spindle=5090
Accel_Spindle=5091
SpeedPercentage_Spindle=92

;Z Axis
MaxSpeed_Z=5093
Accel_Z=5094
SpeedPercentage_Z=95

;X Axis
MaxSpeed_X=5096
Accel_X=5097
SpeedPercentage_X=98

;B Axis
MaxSpeed_B=5099
Accel_B=5100
SpeedPercentage_B=50

;==================================== [Sync]
;==================================== AxisId=0
HelixType=0
Revolutions=.3
Distance=10
;Spindle
MaxSpeed_Spindle=5040
Accel_Spindle=5041
SpeedPercentage_Spindle=42

;Z Axis
MaxSpeed_Z=5043
Accel_Z=5044
SpeedPercentage_Z=45

;X Axis
MaxSpeed_X=5046
Accel_X=5047
SpeedPercentage_X=48

;B Axis
MaxSpeed_B=5048
Accel_B=5049
SpeedPercentage_B=49

;==================================== [Rec]
;==================================== AxisId=0
RadialOrAxial=0
;Spindle
MaxSpeed_Spindle=5030
Accel_Spindle=5031
SpeedPercentage_Spindle=32

;Z Axis
MaxSpeed_Z=5033
Accel_Z=5034
SpeedPercentage_Z=35

;X Axis
MaxSpeed_X=5036
Accel_X=5037
SpeedPercentage_X=38

;B Axis
MaxSpeed_B=5039
Accel_B=5040
SpeedPercentage_B=39

;Radial
Radial_Waves=5
Radial_Spindle_Amplitude=20 Radial_Axis_Distance=5

;Axial
Axial_Waves=4
Axial_Spindle_Degrees=25
Axial_Axis_Amplitude=7

;==================================== [Grk]
;==================================== AxisId=0
FileOrPattern=0
;Spindle
MaxSpeed_Spindle=5020
Accel_Spindle=5021
SpeedPercentage_Spindle=22

;Z Axis
MaxSpeed_Z=5023
Accel_Z=5024
SpeedPercentage_Z=25

;X Axis
MaxSpeed_X=5026
Accel_X=5027
SpeedPercentage_X=28

;B Axis
MaxSpeed_B=5028
Accel_B=5029
SpeedPercentage_B=29

;Pattern page
RadialOrAxial_Pattern=0
;4a: 2 4b: 3 3a: 6 3b: 7 2a: 4 2b: 5 PatternType=4
Pattern_PatternsPer360=8
Pattern_PatternCount=1
Pattern_SegmentLength=1

;File page
RadialOrAxial_File=0
File_PatternsPer360=7
File_PatternCount=1
File_SegmentLength=1

;Segments: 2 Actual: 3
File_SegmentsOrActual=2

;==================================== [Geo]
;==================================== AxisId=0
RadialOrAxial=0
Rose_n=7
Rose_d=5

;Spindle
MaxSpeed_Spindle=5010
Accel_Spindle=5011
SpeedPercentage_Spindle=12

;Z Axis
MaxSpeed_Z=5013
Accel_Z=5014
SpeedPercentage_Z=15
RadialAmplitude_Z=2
AxialAmplitude_Z=2.5

;X Axis
MaxSpeed_X=5016
Accel_X=5017
SpeedPercentage_X=18
RadialAmplitude_X=2
AxialAmplitude_X=2.5

;B Axis
MaxSpeed_B=5018
Accel_B=5019
SpeedPercentage_B=19
RadialAmplitude_B=3
AxialAmplitude_B=3.5

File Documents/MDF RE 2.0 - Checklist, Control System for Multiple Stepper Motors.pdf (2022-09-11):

## Control System for Multiple Stepper Motors Setup and System Checkout

System For
Checked by
Date
Step | Activity | ✓
1 System Load
1.1 | Load Teensy program Software Teensy Model Version Loaded
1.2 | Load Nextion configuration Software Nextion Model Version Loaded
1.3 | Load Teensy INI file

2 Main Function
2.1 | Spindle move
2.2 | Z axis move
2.3 | X axis move
2.4 | B axis move
3 One Function
3.1 | Spindle move
3.2 | Z axis move
3.3 | X axis move
3.4 | B axis move
4 Index Function
4.1 | Index by Divisions – 4
4.2 | Index by Divisions – 8
5 Move Function
5.1 | Z axis move
5.2 | X axis move
Setup | Move
Limits | Program
Returns | Sync
Main | Recip
One | GreekKey
Index | Rose

Step | Activity | ✓
5.3 | B axis move
6 Sync Function
6.1 | Z axis | Helix type Left | CCW
6.2 | Z axis | Helix type Right | CCW
6.3 | Z axis | Helix type Left | CW
6.4 | X axis | Helix type Left | CCW
6.5 | X axis | Helix type Right | CCW
6.6 | B axis | Helix type Left | CCW
6.7 | B axis | Helix type Right | CCW
7 Recip Function
7.1 | Z axis | Radial | Pattern 1 | CCW
7.2 | Z axis | Radial | Pattern 2 | CCW
7.3 | Z axis | Radial | Pattern 3 | CCW
7.4 | Z axis | Radial | Pattern 1 | CW
7.5 | Z axis | Axial | Pattern 1 | CCW
7.6 | Z axis | Axial | Pattern 2 | CCW
7.7 | Z axis | Axial | Pattern 3 | CCW
7.8 | X axis | Radial | Pattern 1 | CCW
8 Greek Key Function
8.1 | Radial axis runs – 2a pattern
8.2 | Radial axis runs – 2b pattern
8.3 | Axial axis runs – 2a pattern
9 Limit & Estop Switches
9.1 | Limit Switch Pin #
9.2 | Limit Switch Pin #
9.3 | Limit Switch Pin #
9.4 | Limit Switch Pin #
9.5 | E-Stop Switch Pin #

Comments:

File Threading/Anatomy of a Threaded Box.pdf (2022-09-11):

## Anatomy of a Threaded Box


John Swanson’s Turning Threaded Boxes is the best reference for this activity.

- 16 threads / inch (TPI) is the
recommended pitch. Experienced turners have cited this as good for most woods.

For 60° threads, the threads are
- 0.040” wide and
- 0.054” tall.
- The division between a box’s base and lid as advocated by John is shown to the right.
- The recommended approach is to thread the lid 1st, and then thread the base. This allows the lid to be used to ensure the threading is proper on the base.
- Another recommendation is to turn a set of blocks with the same internal and external threads. These blocks can then be used to hold the mated parts whilst finishing the ends. This is particularly useful if the pieces are held by a tenon in a collet chuck.

40%

60%

Threaded Box’s Lid; Width needs to be greater for fragile woods like burls. Consider 1/8” to 1/4”.; Width of relief should equal width of one thread (Thread Pitch width); One option for aligning the grain (after both pieces are threaded is to remove some of this edge.; Be careful: if it is off by 90º, then the amount to be removed is only 25% of one thread’s width.; With 16 TPI, this is:; Width of threaded area needs to be 4-5 threads. This will hold sufficiently, and more would make attaching the lid too onerous to attach to the body.; 45º chamfer added to ease getting the lid on and off

Hand-chased threads need a relief here. For threads cut with a jig or using a cutter held in a drilling spindle do not need such a relief.


## Threaded Box’s Base

Width of threaded area needs to be 3-4 threads. This will hold sufficiently, and more would make attaching the lid too onerous to attach to the body.

If the fit of the lid is too tight, additional threads are needed.

Width of relief
should equal
width of one
thread (Thread
Pitch width)

A second option for aligning the grain (after both pieces are threaded is to remove some of this shoulder. This is the preferred approach.

As noted above, be careful.

45º chamfer added to ease
getting the lid on and off

Hand-chased threads need a relief here. For threads cut with a jig or using a cutter held in a drilling spindle do not need such a relief, except for space for the nose of the cutter.

Width needs to be greater for fragile woods like burls. Consider 1/8” to 1/4”.

Starting diameter for this tenon is 0.060” greater than the internal diameter of the lid.

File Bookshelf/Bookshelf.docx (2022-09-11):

Handbook


Sharpening

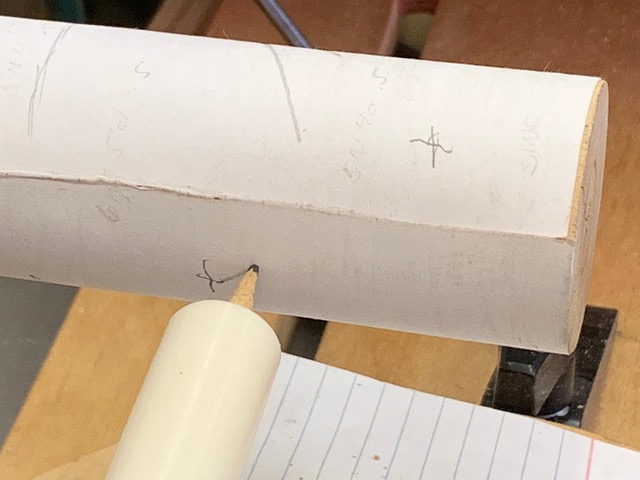
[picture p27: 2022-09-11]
NextionPreV22/Images/PaperChuck-Pumping2.jpg

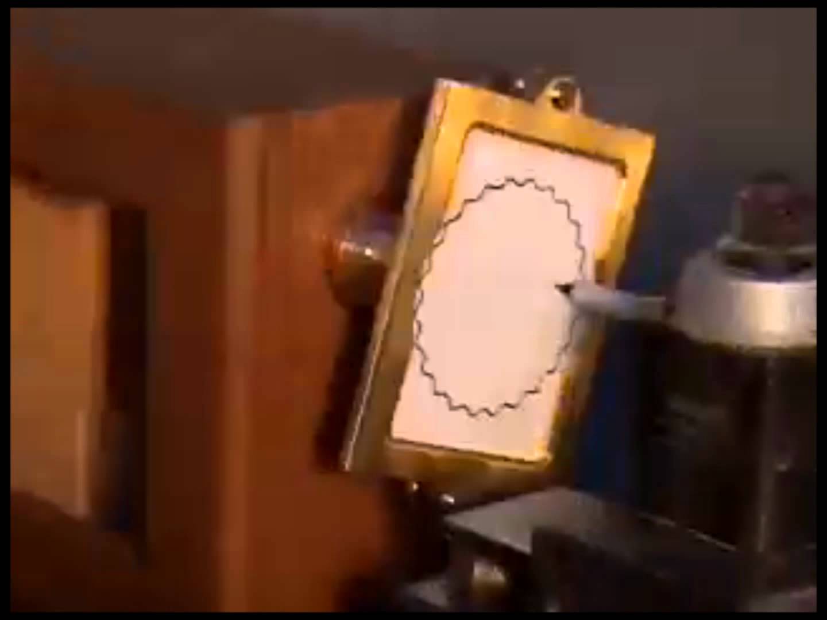
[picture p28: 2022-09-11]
NextionPreV22/Images/PaperChuck.jpg

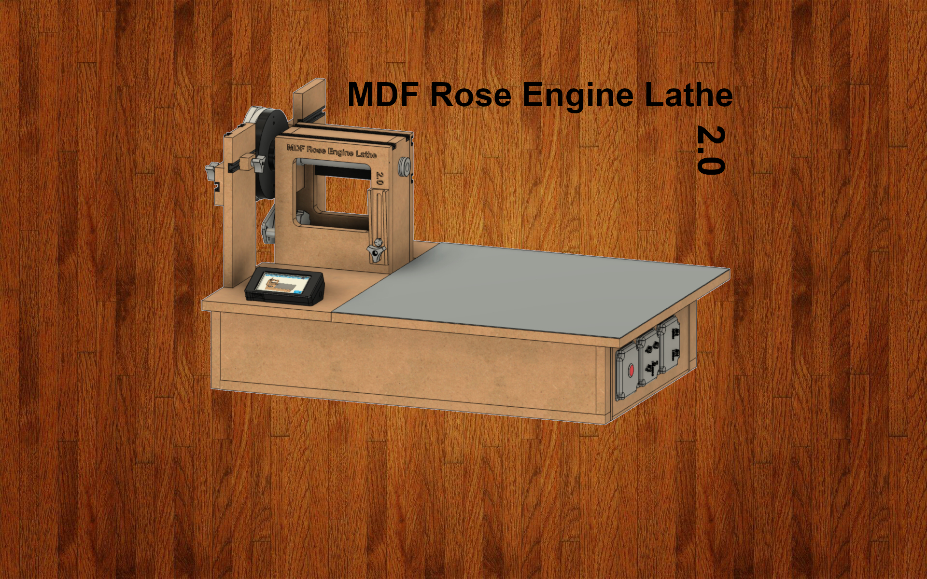
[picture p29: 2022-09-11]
NextionPreV22/Images/MDF Rose Engine Lathe Wallpaper.jpg

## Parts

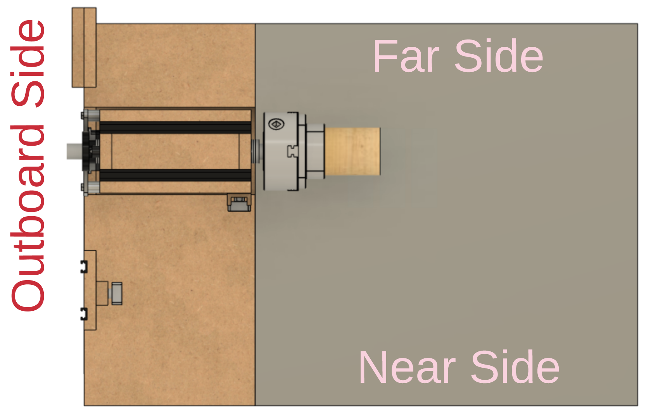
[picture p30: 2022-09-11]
ELFOSv4/Images/Nomenclature2.png

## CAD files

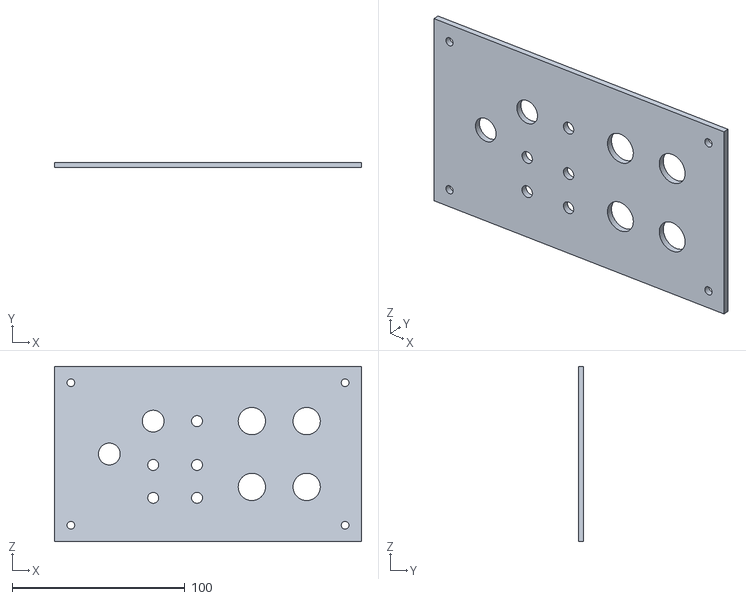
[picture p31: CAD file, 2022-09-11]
3DPrint-MSMCS/Controls Face Plate.stl
177.8 x 3.17 x 101.6

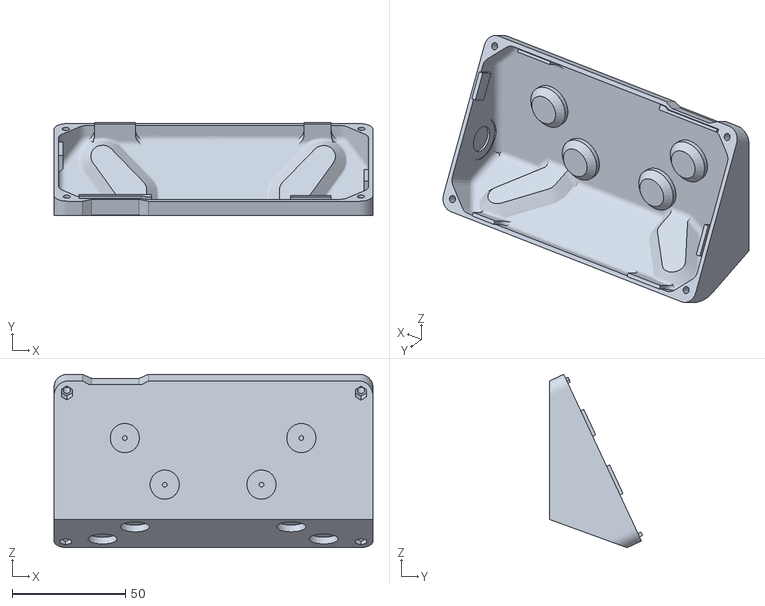
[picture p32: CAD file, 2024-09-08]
3Dprint/Nextion 4.3e Base.stl
141.0 x 41.2 x 76.6

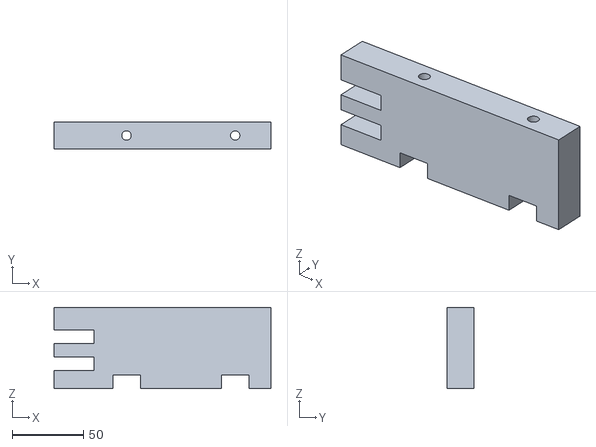
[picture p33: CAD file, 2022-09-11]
Images/AA-Alignment-Block.stl
152.4 x 19.1 x 57.2

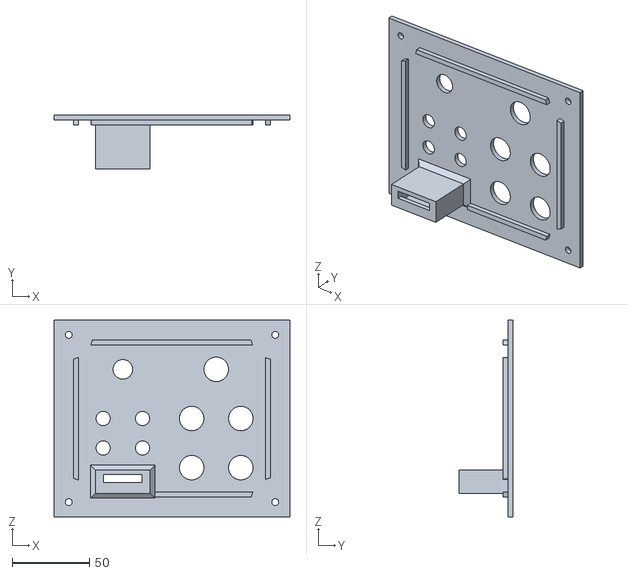
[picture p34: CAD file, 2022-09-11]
3DPrint-MSMCS/MDF RE 2.0 Cntrls Faceplate 1.stl
152.4 x 34.6 x 127.0

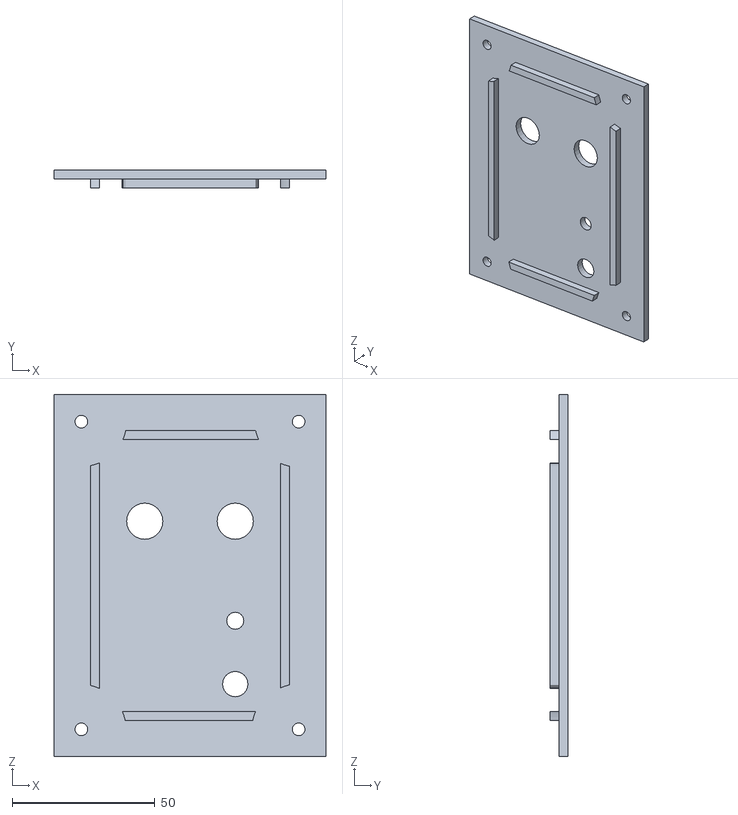
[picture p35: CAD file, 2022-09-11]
3DPrint-MSMCS/MDF RE 2.0 Cntrls Faceplate 2.stl
95.3 x 6.35 x 127.0

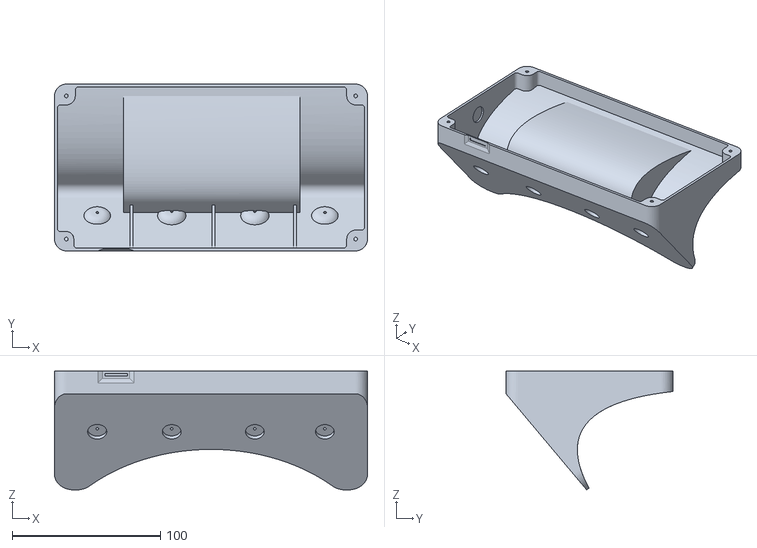
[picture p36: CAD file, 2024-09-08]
3Dprint/Nextion 7i v2 Base - Angle.stl
210.9 x 112.4 x 80.2

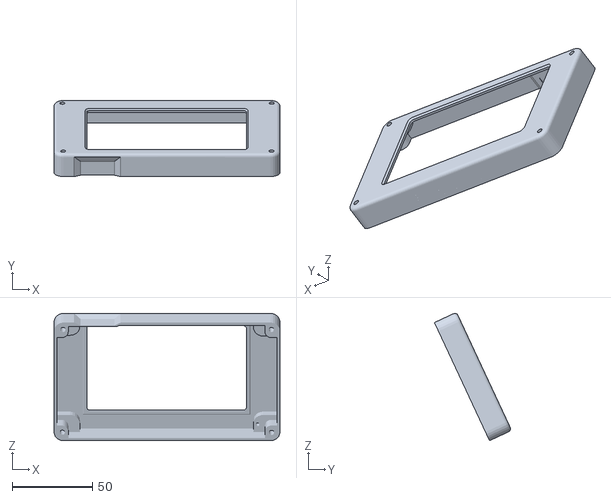
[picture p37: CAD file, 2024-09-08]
3Dprint/Nextion 4.3e Bezel.stl
141.1 x 47.6 x 79.6

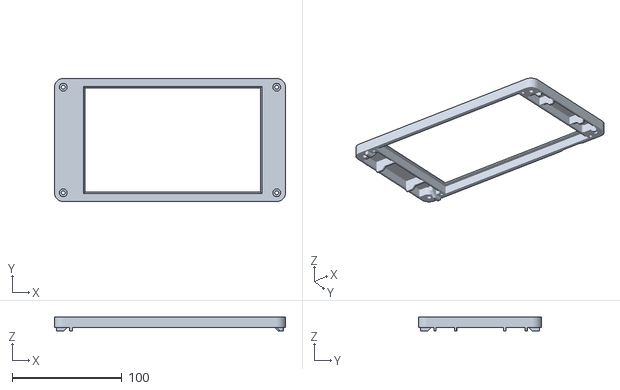
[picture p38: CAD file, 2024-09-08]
3Dprint/Nextion 7i v2 Bezel.stl
210.9 x 112.4 x 12.5

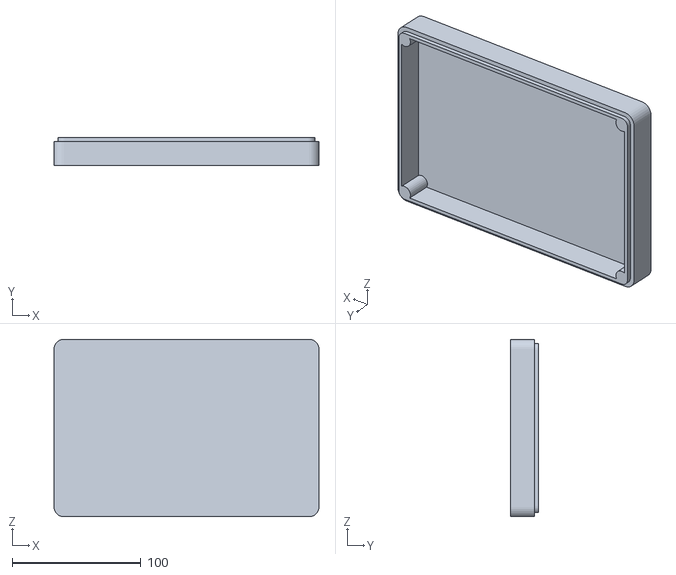
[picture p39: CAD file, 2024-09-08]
3Dprint/Nextion 7i v1 Base - Flat.stl
205.8 x 22.1 x 137.8

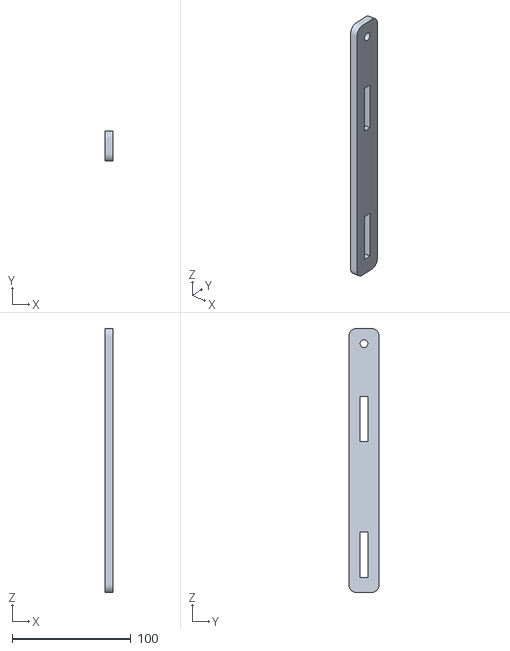
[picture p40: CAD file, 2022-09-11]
3Dprint/AA3-Horizontal-Bar.stl
6.35 x 25.4 x 222.2

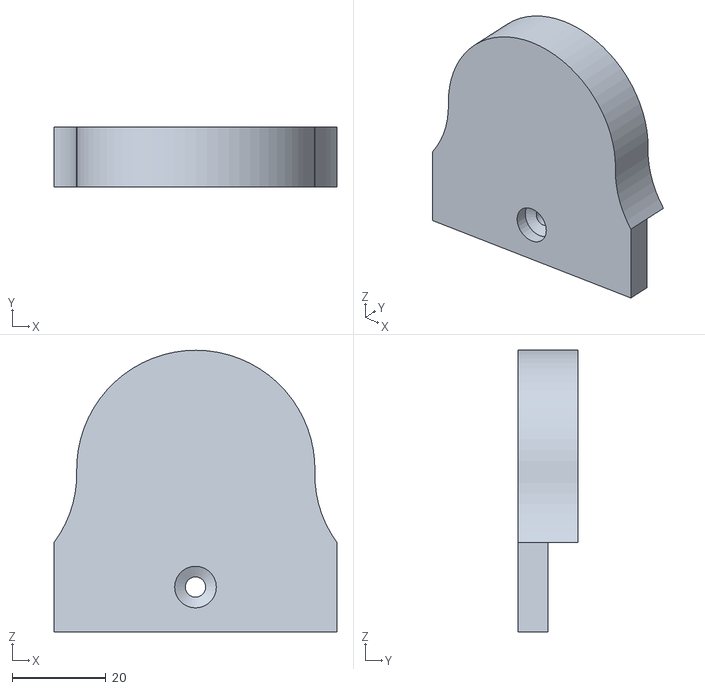
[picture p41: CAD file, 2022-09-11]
3Dprint/AA-Round-2in-Rubber.stl
60.3 x 12.7 x 60.0

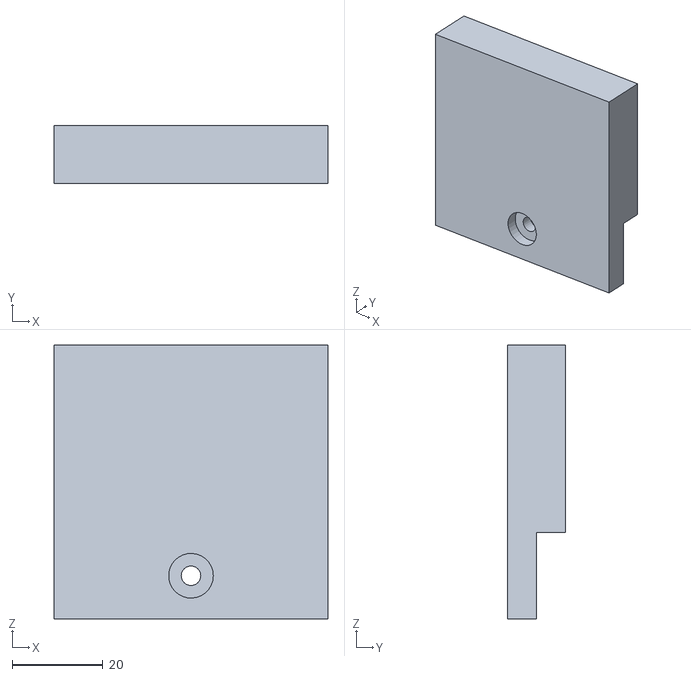
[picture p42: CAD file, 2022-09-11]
3Dprint/AA-Flat-Rubber.stl
60.3 x 12.7 x 60.3

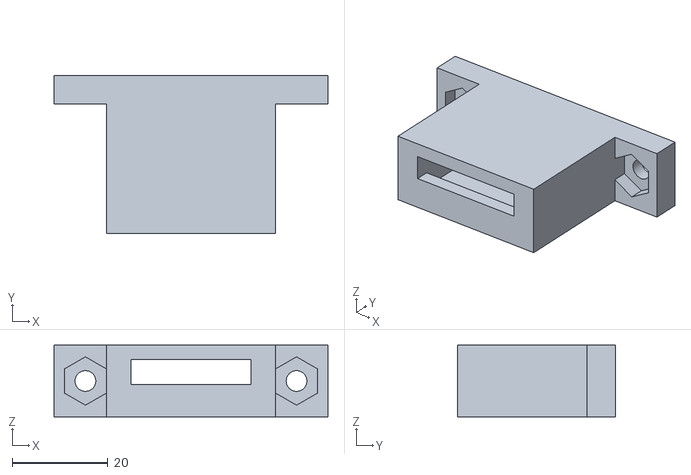
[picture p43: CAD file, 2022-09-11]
3Dprint/microSD Holder.stl
57.1 x 33.0 x 15.0

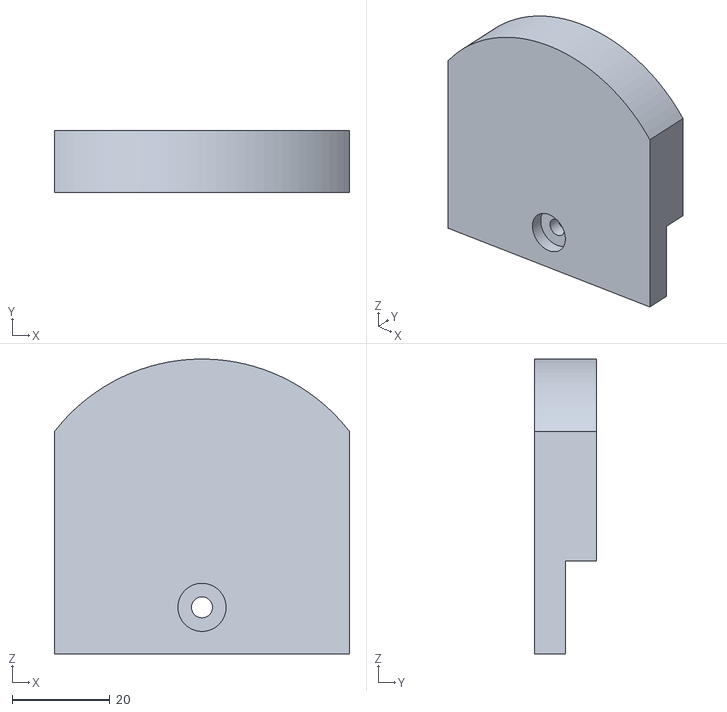
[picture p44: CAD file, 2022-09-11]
3Dprint/AA-Round-Rubber.stl
60.3 x 12.7 x 60.3

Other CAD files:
3Dprint/ELFOS-Face-Plate-Controls-v4.stl
3Dprint/ELFOS-Face-Plate-Power-v4.stl
3Dprint/NextionCaseBezel v2.stl
3Dprint/ Curv-LimSwBase.stl
3Dprint/AA Rear Rubber.stl
3Dprint/AA-Align-Blk-v1.stl
3Dprint/AA-Align-Blk-v2.stl
3Dprint/AA-Alignment-Block.stl
3Dprint/AA-Point-Rubber-1.stl
3Dprint/AA-Point-Rubber-2.stl
3Dprint/AA-Point-Rubber.stl
3Dprint/AA-Round-1in-Rubber.stl
3Dprint/AA-Round-3in-Rubber.stl
3Dprint/AA-Rubber-Spacer.stl
3Dprint/AA-Rubber.stl
3Dprint/AA-Rubbers.f3d
3Dprint/AA-Rubbers.stl
3Dprint/AA-Spacer-Blk-v1.stl
3Dprint/AA-Spacer-Blk-v2.stl
3Dprint/AA-Vertical-Bar Spacer1.stl
3Dprint/AA-Vertical-Bar Spacer2.stl
3Dprint/AA4-Vertical-Bar.stl
3Dprint/Controls Face Plate v2.f3d
3Dprint/Controls Face Plate v2.stl
3Dprint/Controls Face Plate v3.f3d
3Dprint/Controls Face Plate v3.stl
3Dprint/Curv-LimSwHolder.stl
3Dprint/Curv-LimSwL.stl
3Dprint/Curv-LimSwR.stl
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

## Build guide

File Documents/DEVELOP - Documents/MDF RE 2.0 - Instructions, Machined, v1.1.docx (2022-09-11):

MDF Rose Engine Lathe 2.0

with Stepper Motor Drive

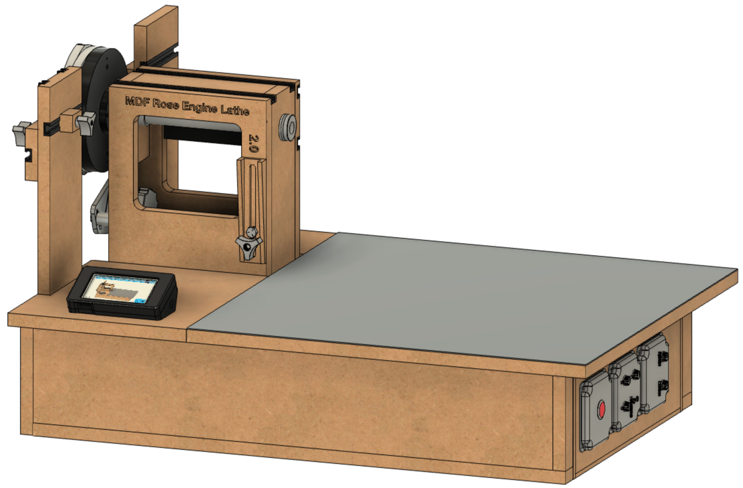
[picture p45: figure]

Machined Parts for the

Base & Headstock

Version 1.0

23 March 2021

This document is intended to help one unfamiliar with the MDF rose engine to build one easily. It is designed to go with the kit you can purchase from www.ColvinTools.com.

There are some variations from the ideas documented by Jon Magill at www.rogueturner.com. Where this is the case, we have tried to document such changes and provide the reason for the change.

This document is also designed to use a stepper motor for driving the spindle.

If you have any questions, please contact us at ColvinTools@Gmail.com.

Good luck and we hope you enjoy this machine as much as we.

Rich Colvin & Jack Zimmel

# Getting Started

As you get started with building this machine, please consider making the machine exactly according to the outlined instructions. There are lots of ways you can modify this, and, quite frankly, the MDF rose engine encourages experimentation. But it is best to attempt those modifications after understanding how it works. Some ideas which sound grand may not appear so after understanding how the machine works (we speak from experience).

If you have any questions on the terminology in this document, check out the “Ornamental Turning Book of Knowledge” (www.OTBoK.info).

## Accuracy

When making the MDF Rose Engine 2.0, these parts must be made quite accurately.

# Spindle Shaft

This is the spindle shaft from the original MDF Rose Engine Lathe. The MDF Rose Engine Lathe 2.0 has a spindle with a Morse taper.

# Spindle Flange

# Stepper Pulley

File for 3D printing at https://github.com/elfren/RoseEngine_SpindleAndAxis/tree/master/Hardware/GT2-5mm-108t.

# Bungee Block

# Bungee Button

# Rear Stop Block

# Fading Wedge

# Double Rubbers

# Stepper Motor Mount Bracket

### Off-the-shelf Parts:

4 - #8-32 x 3/8" screws (Phillips or BHCS) for NEMA 23 motor

2 - 1/4"-20 x 2-1/2" Hex head bolts

3 - 1/4" washers, 2 for plate and 1 for idler

1 - 1/4"-20 x 5/8" FH hex drive screw

1 - 1/4"-20 x 3/8" BHCS

2 - 1/4"-20 dowel nuts for wood (.39" OD x .63" L) McM-C #90835A210 https://www.mcmaster.com/90835A210/

1 - 12T GT2 5mm pulley with .25" bore, 2 flanges, aluminum, for 9mm wide belt, SDP-SI #A 6A55-012DF0908 http://shop.sdp-si.com/catalog/product/?id=A%206a55-012df0908

2 - 3/8" x 7/8" x 9/32" shielded ball bearings MSC #01377498 https://www.mscdirect.com/product/details/01377498

1 - GT3 5mm pitch, 131T / 655mm long, 9mm wide Timing belt, Misumi #GBN655EV5GT-90 https://us.misumi-ec.com

### Manufactured Parts:

1 - Stepper Plate - 1/4" thick plate, rough 5-3/4" x 3-1/4"

2 - Stepper plate spacers - 3/4" diameter aluminum rod

1 - Idler shaft - 7/8" diameter steel rod

1 - Idler shaft spacer - 5/8" diameter HDPE rod or similar

1 - Idler body - 1-1/4" diameter HDPE rod or similar

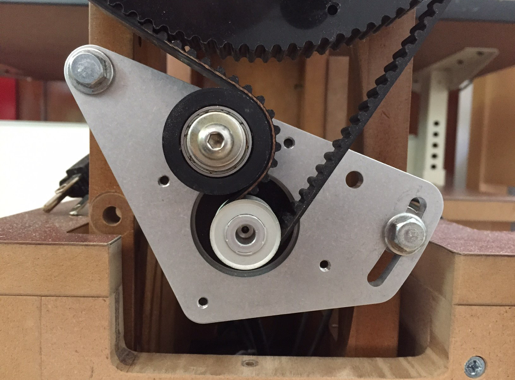
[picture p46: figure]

To the extent that material may appear to be infringed, we assert that such alleged infringement is permissible under fair use principles in U.S. copyright laws. If you believe material has been used in an unauthorized manner, please contact me at ColvinTools@Gmail.com.

Portions of this document are copyrighted by Jon Magill and are used with his permission.

Permission is not granted to manufacture these for sale.

MDF Rose Engine Lathe 2.0 Machined Parts for the Base & Headstock

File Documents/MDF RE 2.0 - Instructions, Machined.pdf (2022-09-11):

# MDF Rose Engine Lathe 2.0

# with Stepper Motor Drive


# Machined Parts for the Base & Headstock

## Version 1.0 23 March 2021

## MDF Rose Engine Lathe 2.0 Machined Parts for the Base & Headstock

This document is intended to help one unfamiliar with the MDF rose engine to build one easily. It is designed to go with the kit you can purchase from www.ColvinTools.com.

There are some variations from the ideas documented by Jon Magill at www.rogueturner.com. Where this is the case, we have tried to document such changes and provide the reason for the change.

This document is also designed to use a stepper motor for driving the spindle.

If you have any questions, please contact us at ColvinTools@Gmail.com.

Good luck and we hope you enjoy this machine as much as we.

Rich Colvin & Jack Zimmel

## Machined Parts for the Base & Headstock

### Table of Contents

## Machined Parts for the Base & Headstock

## Getting Started

As you get started with building this machine, please consider making the machine exactly according to the outlined instructions. There are lots of ways you can modify this, and, quite frankly, the MDF rose engine encourages experimentation. But it is best to attempt those modifications after understanding how it works. Some ideas which sound grand may not appear so after understanding how the machine works (we speak from experience).

If you have any questions on the terminology in this document, check out the “Ornamental Turning Book of Knowledge” (www.OTBoK.info).

### Accuracy

When making the MDF Rose Engine 2.0, these parts must be made quite accurately.

## Machined Parts for the Base & Headstock

## Spindle Shaft

This is the spindle shaft from the original MDF Rose Engine Lathe. The MDF Rose Engine Lathe 2.0 has a spindle with a Morse taper.

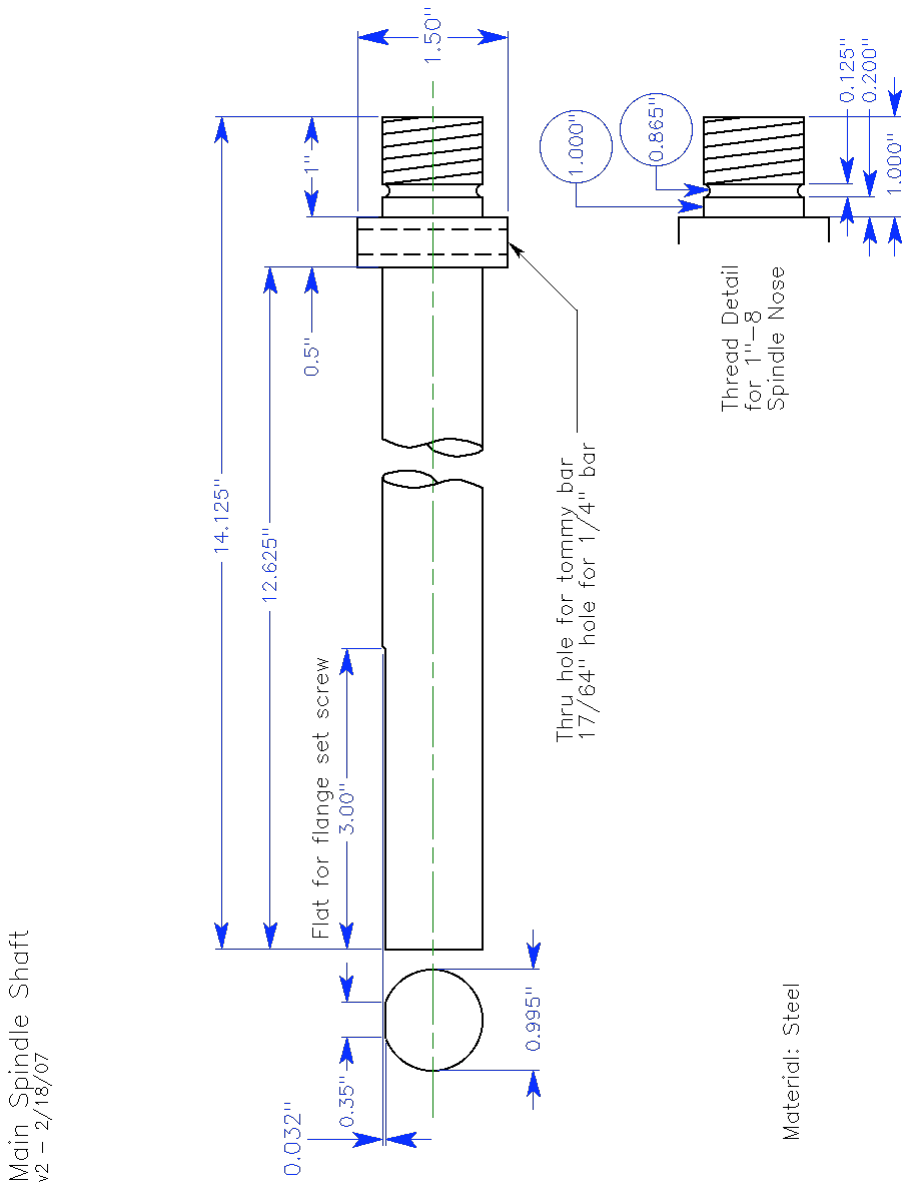
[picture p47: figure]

— 7 — | © Copyright 2007, All rights reserved

## Machined Parts for the Base & Headstock

## Spindle Flange

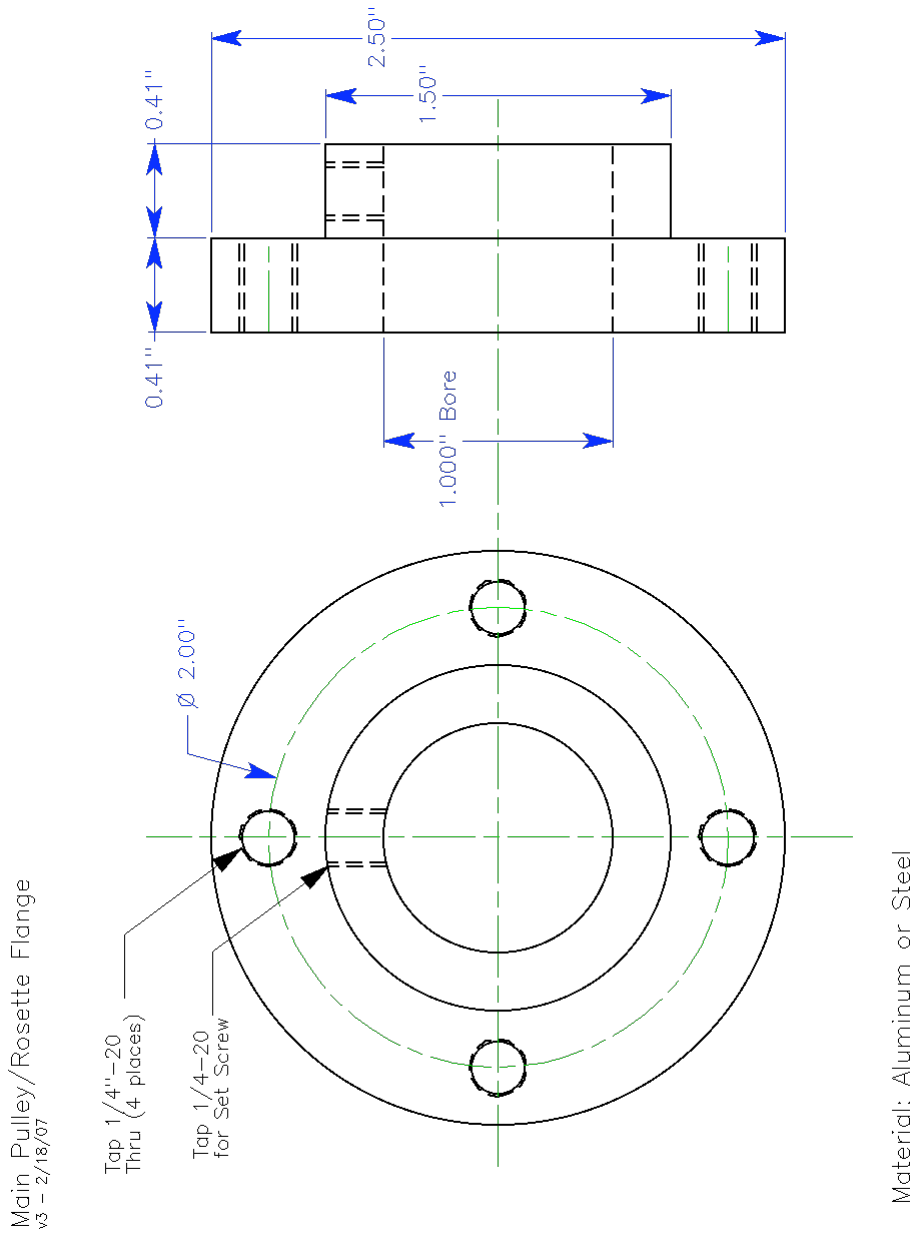
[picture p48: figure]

— 8 — | © Copyright 2007, All rights reserved

## Machined Parts for the Base & Headstock

## Stepper Pulley

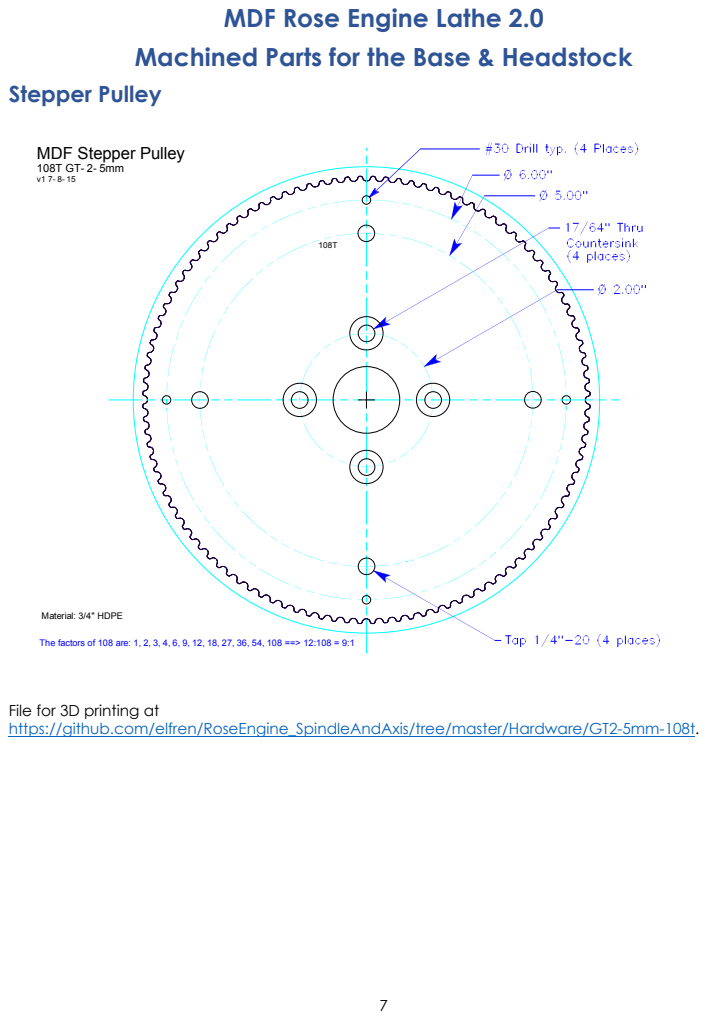
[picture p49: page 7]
Material: 3/4" HDPE

MDF Stepper Pulley

The factors of 108 are: 1, 2, 3, 4, 6, 9, 12, 18, 27, 36, 54, 108 ==> 12:108 = 9:1

File for 3D printing at
https://github.com/elfren/RoseEngine_SpindleAndAxis/tree/master/Hardware/GT2-5mm-108t.

## Machined Parts for the Base & Headstock

## Bungee Block

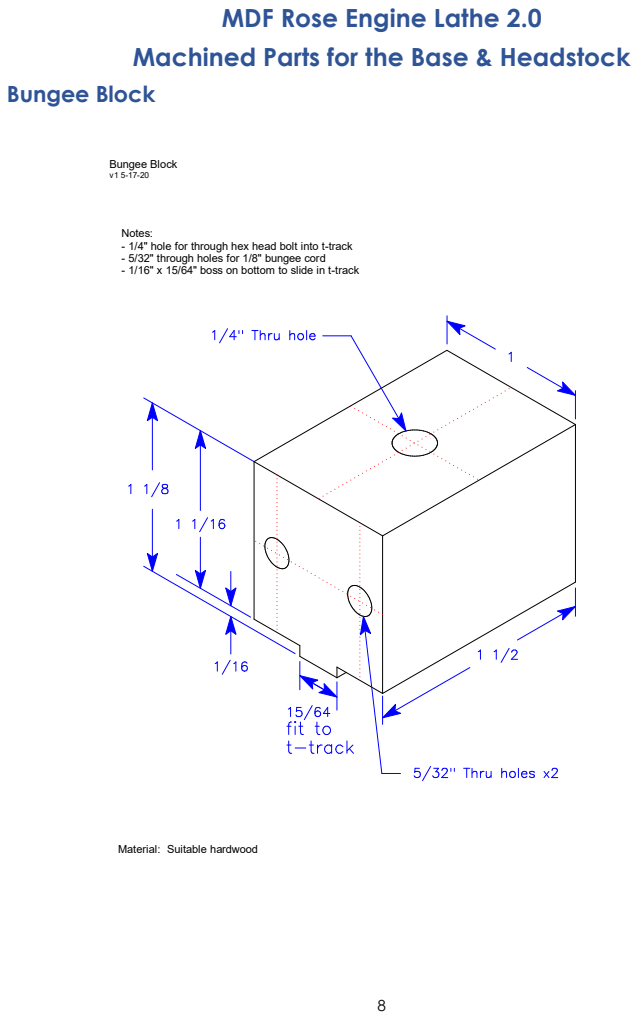
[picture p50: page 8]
Bungee Block v1 5-17-20

Notes:
- 1/4" hole for through hex head bolt into t-track
- 5/32" through holes for 1/8" bungee cord
- 1/16" x 15/64" boss on bottom to slide in t-track

Material: Suitable hardwood

## Machined Parts for the Base & Headstock

## Bungee Button

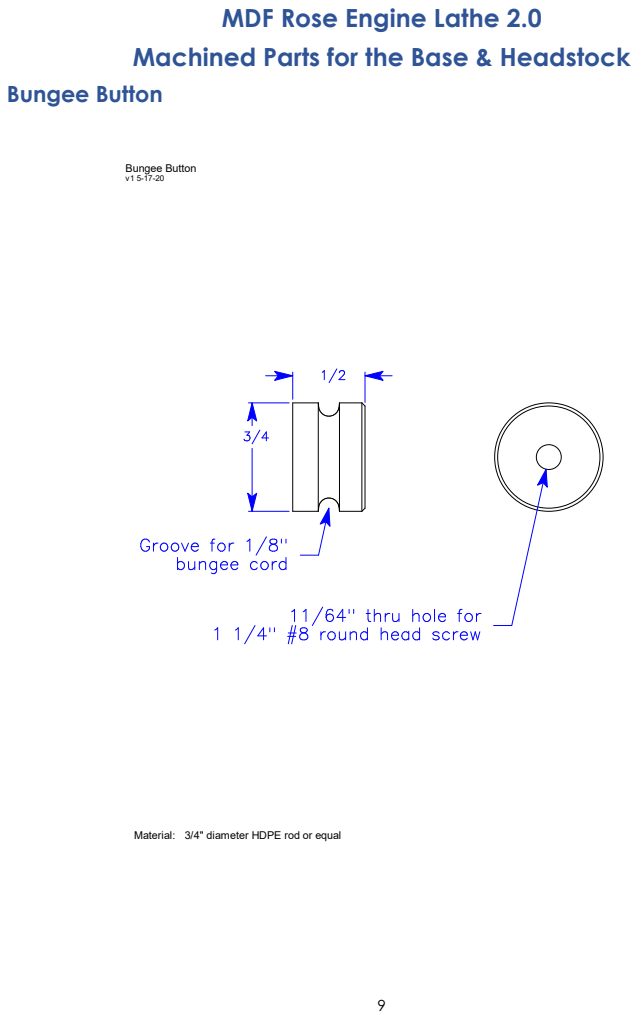
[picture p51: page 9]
Bungee Button v1 5-17-20

Material: 3/4" diameter HDPE rod or equal

## Machined Parts for the Base & Headstock

## Rear Stop Block

Rear Stop Block
v2 5-17-20

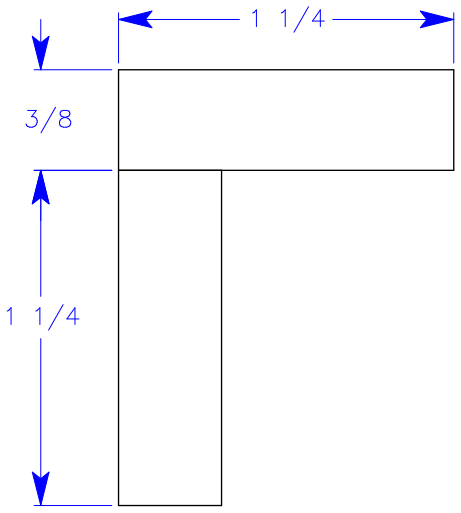
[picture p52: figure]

Material: Suitable hardwood

Notes:
- Made from strip of 1 1/4" x 3/8" stock
- Glue and pin nail strips, then cut to length

## Machined Parts for the Base & Headstock

## Fading Wedge

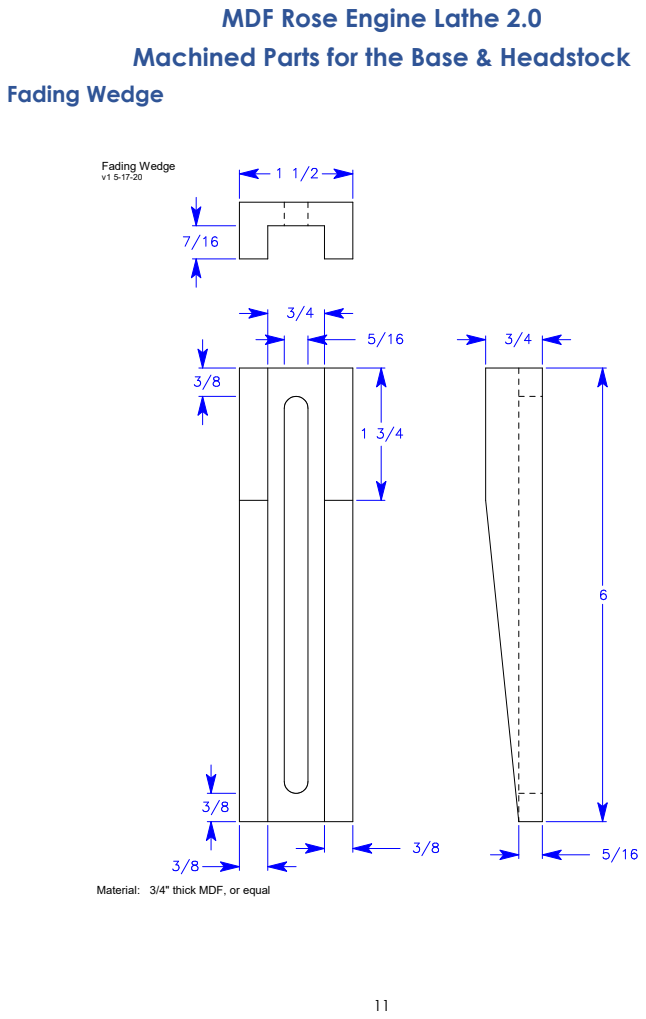
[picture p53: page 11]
Fading Wedge v1 5-17-20

Material: 3/4" thick MDF, or equal

## Machined Parts for the Base & Headstock

## Double Rubbers

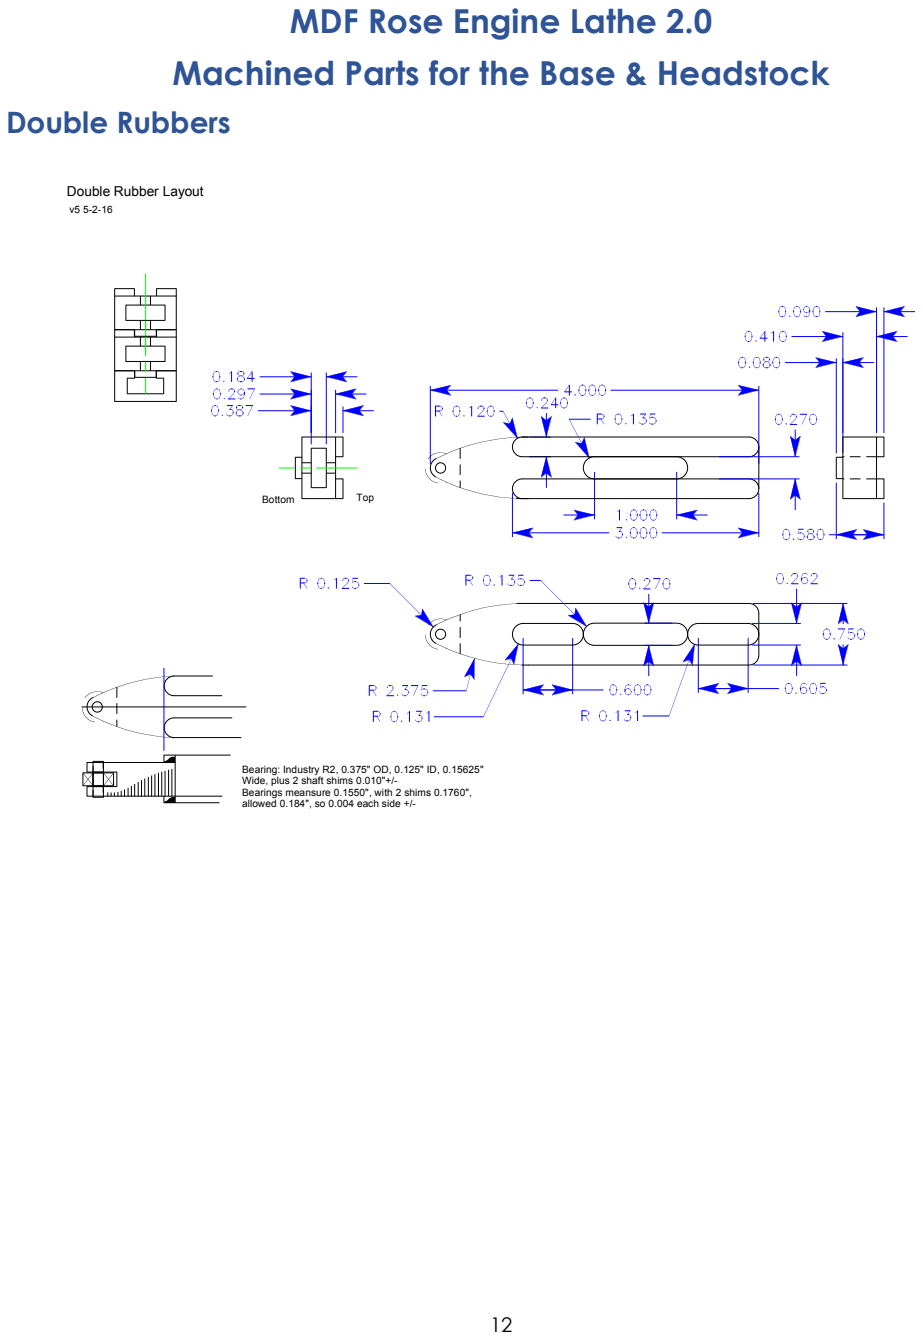
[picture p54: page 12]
Bottom; Top

Double Rubber Layout

Bearing: Industry R2, 0.375" OD, 0.125" ID, 0.15625"
Wide, plus 2 shaft shims 0.010"+/-
Bearings meansure 0.1550", with 2 shims 0.1760",
allowed 0.184", so 0.004 each side +/-

## Machined Parts for the Base & Headstock

Double Rubber Parts_v3 | 11/14/20, 2:59 PM

Double Rubber Parts for MDF Rose Engine “Double Rubber Kit”
- v1 — 6-19-15
- v2 - 8-3-15
- v3 - 11-14-20 - updated comments for Rich Colvin, Jack Zimmel

One “Double Rubber” kit consists of:

- 2 rubbers made up from:
- Anodized aluminum rubber bodies x2
- Bearings x2
- Shaft shims x4
- Dowel pins x2
- 2 long thumbscrews - now replaced by a pre-assembled part, see below
- 1/4”-20 x 1.5”L SHCS x2
- Pressed on knobs x2
- 1 spindle shim (no longer needed with update, see below)

Components required to make Double Rubber “kits”:

Rubbers
- Raw material — 6061 aluminum 3/4” x 3/4” rectangular bar (or 5/8” x 3/4” if available)
- Finished part is 4” long, so rough cut allowance of 4-1/4”, minus kerf, figure 4-1/2”
- Yield from:
6’ stick = 16 pieces, or 8 kits
12’ stick = 32 pieces, or 16 kits (normal aluminum stick length)
20’ stick = 53 pieces, or 26 kits

Dowel pins — (Note: each batch has to be mic’ed to select slightly undersized pins)
- 1/8” dia. x 7/16” long
- Alloy Steel Dowel Pin, 1/8" Diameter, 7/16" Length
- McMaster-Carr part #98381A218 $13.95 per pack of 100 as of 11-14-20

Bearings
- Industry size R2-2Z, double shielded, for 1/8” shaft & 3/8” OD, 5/32” wide
- Steel Ball Bearing, ABEC-1, Double Shielded, R2 for 1/8" Shaft Diameter, 3/8" OD
- McMaster-Carr part: #60355K41, $6.56 Each as of 11-14-20

Shaft Shims for Bearings
- For shaft size 0.125” x 0.010” thick

## Machined Parts for the Base & Headstock

## Stepper Motor Mount Bracket

Off-the-shelf Parts:

4 - #8-32 x 3/8" screws (Phillips or BHCS) for NEMA 23 motor 2 - 1/4"-20 x 2-1/2" Hex head bolts
3 - 1/4" washers, 2 for plate and 1 for idler
1 - 1/4"-20 x 5/8" FH hex drive screw
1 - 1/4"-20 x 3/8" BHCS

2 - 1/4"-20 dowel nuts for wood (.39" OD x .63" L) McM-C #90835A210 https://www.mcmaster.com/90835A210/

1 - 12T GT2 5mm pulley with .25" bore, 2 flanges, aluminum, for 9mm wide belt, SDP-SI #A 6A55-012DF0908 http://shop.sdp-si.com/catalog/product/?id=A%206a55-012df0908

2 - 3/8" x 7/8" x 9/32" shielded ball bearings MSC #01377498 https://www.mscdirect.com/product/details/01377498

1 - GT3 5mm pitch, 131T / 655mm long, 9mm wide Timing belt, Misumi #GBN655EV5GT-90 https://us.misumi-ec.com

Manufactured Parts:

1 - Stepper Plate - 1/4" thick plate, rough 5-3/4" x 3-1/4" 2 - Stepper plate spacers - 3/4" diameter aluminum rod 1 - Idler shaft - 7/8" diameter steel rod
1 - Idler shaft spacer - 5/8" diameter HDPE rod or similar 1 - Idler body - 1-1/4" diameter HDPE rod or similar

## Machined Parts for the Base & Headstock

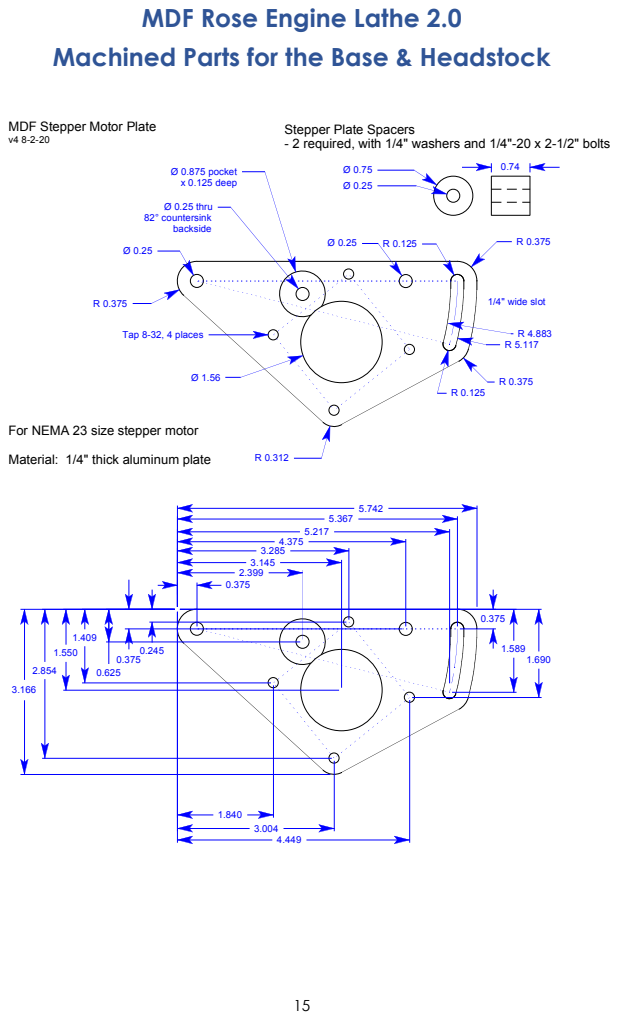
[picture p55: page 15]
Ø 0.25 thru; Ø 0.875 pocket; Tap 8-32, 4 places; 82° countersink backside; x 0.125 deep; 1/4" wide slot

MDF Stepper Motor Plate v4 8-2-20

Stepper Plate Spacers
- 2 required, with 1/4" washers and 1/4"-20 x 2-1/2" bolts

For NEMA 23 size stepper motor

Material: 1/4" thick aluminum plate

## Machined Parts for the Base & Headstock

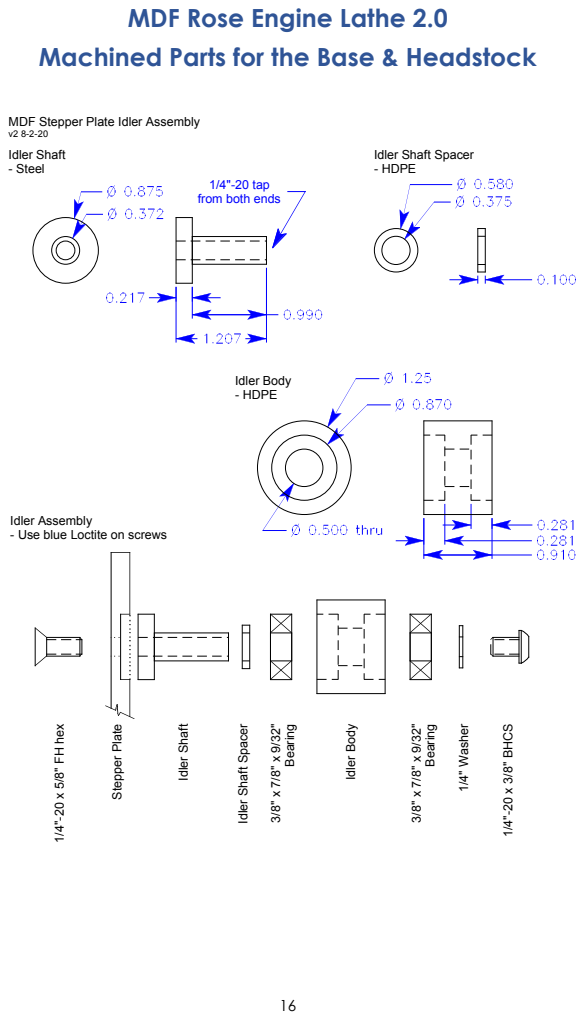
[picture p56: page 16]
Idler Shaft - Steel; Idler Body - HDPE; 1/4"-20 x 5/8" FH hex; Stepper Plate; Idler Shaft; Bearing; Idler Body; 1/4" Washer

MDF Stepper Plate Idler Assembly v2 8-2-20

Idler Shaft Spacer
- HDPE

1/4"-20 tap
from both ends

Idler Assembly
- Use blue Loctite on screws

## Machined Parts for the Base & Headstock

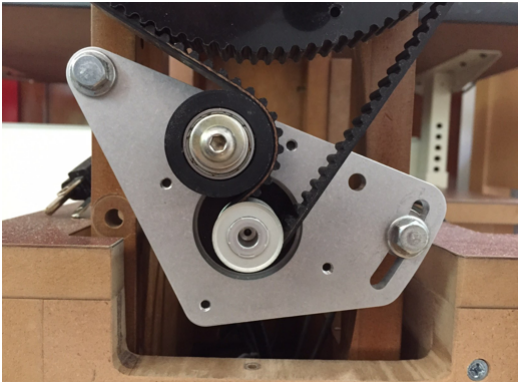
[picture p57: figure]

## Machined Parts for the Base & Headstock

To the extent that material may appear to be infringed, we assert that such alleged infringement is permissible under fair use principles in U.S. copyright laws. If you believe material has been used in an unauthorized manner, please contact me at ColvinTools@Gmail.com.

Portions of this document are copyrighted by Jon Magill and are used with his permission.

Permission is not granted to manufacture these for sale.

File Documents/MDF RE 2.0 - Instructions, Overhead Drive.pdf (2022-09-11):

# MDF Rose Engine Lathe 2.0

# with Stepper Motor Drive

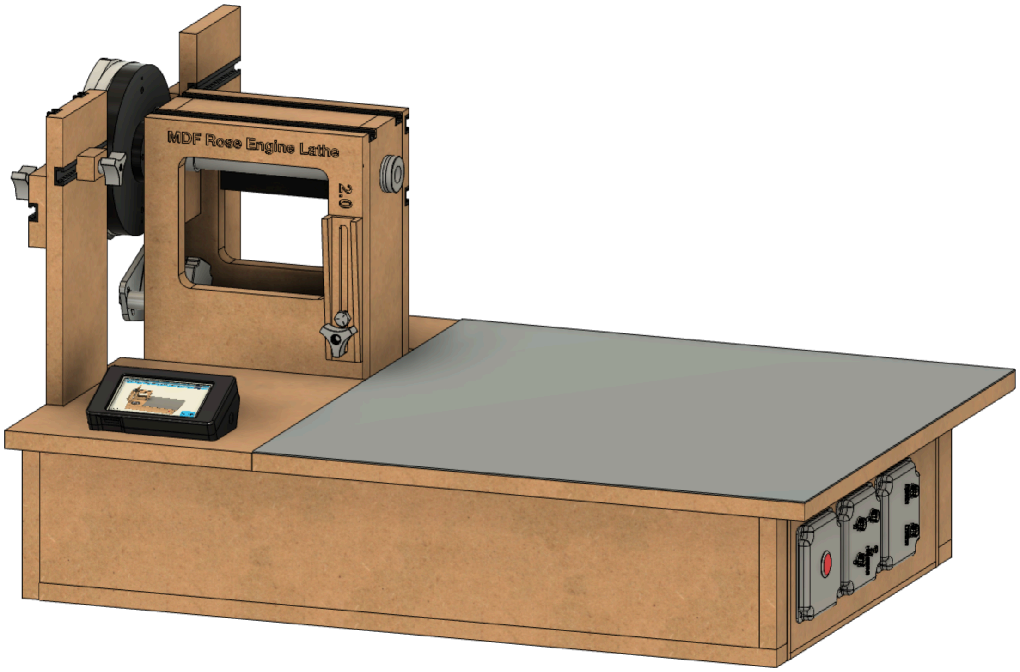
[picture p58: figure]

# Instructions for Building the Overhead Drive

## Version 0.1 17 August 2020

## MDF Rose Engine Lathe 2.0 Installation Instructions – Overhead Drive

This document is intended to help one unfamiliar with the MDF rose engine to build one easily. It is designed to go with the kit you can purchase from www.ColvinTools.com.

If you have any questions, please contact us at ColvinTools@Gmail.com.

Good luck.

Rich Colvin & Jack Zimmel

## Installation Instructions – Overhead Drive

### Table of Contents

Cautions | Error! Bookmark not defined.

## Installation Instructions – Overhead Drive

## Getting Started

As you get started with building this machine, please consider making the machine according to the outlined instructions. There are a boatload of ways you can modify this, and, quite frankly, the MDF rose engine encourages experimentation. But it is best to attempt those modifications after understanding how it works. Some ideas which sound grand may not appear so after understanding how the machine works (we speak from experience).

If you have any questions on the terminology in this document, check out the “Ornamental Turning Book of Knowledge” (www.OTBoK.info).

This document outlines the approach for setting up the overhead drive on the MDF Rose Engine Lathe 2.0.

Please also note: Permission is not granted to manufacture these for sale.

## Installation Instructions – Overhead Drive

## Overview

## Installation Instructions – Overhead Drive

To the extent that material may appear to be infringed, we assert that such alleged infringement is permissible under fair use principles in U.S. copyright laws. If you believe material has been used in an unauthorized manner, please contact me at ColvinTools@Gmail.com.

Permission is not granted to manufacture these for sale.

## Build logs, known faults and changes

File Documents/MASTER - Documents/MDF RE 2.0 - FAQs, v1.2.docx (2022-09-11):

MDF Rose Engine Lathe 2.0


Frequently Asked Questions

Version 1.2

08 January 2021

This document is intended to answer frequently asked questions about the rose engine lathe kit sold on www.ColvinTools.com.

If you have any questions, please contact us at ColvinTools@Gmail.com.

Good luck.

Rich Colvin & Jack Zimmel

The questions below are commonly asked, and responses are given to help the reader.

## General

Does this design accommodate both rocking and pumping?

This kit provides for rocking, and there have been a number of people who have adding pumping capabilities. That capability is not provided by this kit at this time.

As we evolve and add to the system features over time, we will evaluate and consider adding it to the system. It will probably come as an add-on to the base system and will not require changes to the design we have delivered.

None-the-less, if you are new to ornamental turning, there are so many capabilities provided by this machine that it will probably be a long time before you find the lack of pumping to be a limitation to your artistic endeavors (at least I haven’t yet).

Does this design accommodate a barrel approach with more than two rosettes?

The use of more than two rosettes at one time is something not accommodated by the design of this lathe. We have spoken with a large number of MDF rose engine lathe users, and none have expressed that having only two rosettes has limited their capabilities.

Instead, the ability to easily switch rosettes is a design feature for this machine. Other unique features for this machine include:

1. The ability to easily change the phasing of the rosettes (vs. the object) without having to perform any calculations.
2. The ability to change the alignment of one rosette against another.

So, if you are new to ornamental turning, this machine will enable you to pursue your artistic endeavors easily and without having to spend great amounts of time learning how.

Where can I learn more about ornamental turning?

There are a number of great good options:

- Join the Ornamental Turners International (http://ornamentalturners.com/). There is a forum on the web site which allows for questions to be posed and are typically answered relatively soon.
- Attend the Ornamental Turners International Symposium. There, you will meet many other users of the MDF rose engine lathe.
- Check out the Ornamental Turning Book of Knowledge (https://www.otbok.info/). There is also a list of additional resources on that site.

## What Do I Need to Get Started?

An MDF rose engine lathe consists of just a few parts, but we have broken up those parts to make it configurable for what you might want to do. The following questions are designed to help you get to the right answers for your situation.

0 | Do you want to buy an off-the-shelf system with nothing required by you to get it up and running? | Yes | Used MDF rose engine lathes do become available from time to time, but not too often. Otherwise, you will need to build one as new MDF rose engine lathes are not sold as an off-the-shelf system. If this is a must for you, look at other options. There are some good ones, and they are listed at Buying a Rose Engine Lathe (https://otbok.info/OT%20-%20Buying%20A%20RE.html) on the Ornamental Turning Book of Turning (https://www.otbok.info/).
| | No | Move on to question 1.

1 | Do you already have one of the original MDF Rose Engine Lathes? (and are willing to cannibalize it for parts) | Yes | Many of the key parts can be moved to the newer design. This includes the - Spindle and spindle bushings - Rosette flange - Pivot points - Rubber & rubber parts - Bungee & bungee parts - Rosettes If you added the stepper motor drive to your machine, those parts can be transferred over also. This includes - Stepper motor mounting bracket with idler and bracket attachment hardware - Spindle pulley - Spindle stepper motor pulley - Spindle drive timing belt - Stepper motor - Stepper motor controls
| | No | You will need the Base System Kit (https://colvintools.com/MDF-RE%202.0-BaseSystemKit.html).

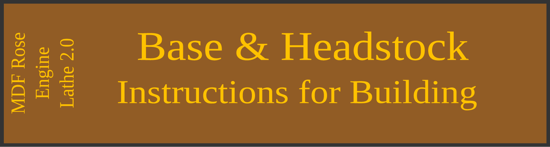
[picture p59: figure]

2 | Do you want to cut the MDF parts yourself? | Yes | Follow the directions outlined in the book to the right. You can get this document at https://mdfre2.colvintools.com/.
| | No | You will need to buy the pre-cut items in the Case Kit (https://colvintools.com/MDF-RE%202.0-CaseKit.html).

3

How do you want to drive the spindle?

Spindle Stepper Motor

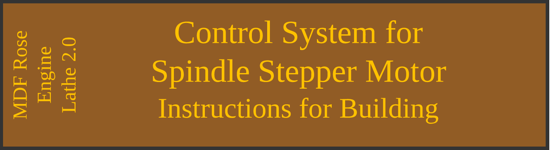
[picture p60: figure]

You will need to buy the Controls Kit - Spindle Stepper Motor (https://colvintools.com/MDF-RE%202.0-ControlsKit-SpindleStepperMotor.html). This kit provides all the parts needed to attach the stepper motor to the headstock, and to drive the spindle.

The other parts you need, and directions to assemble it are outlined in the book above. You can get this document at https://mdfre2.colvintools.com/

- This option is very easy to use.
- Stepper motors deliver consistent torque even at very slow speeds (minutes / revolution).
- It is much lower cost than the option for multiple stepper motors.
- If you take this option, most of the parts are reusable if you later decide to go with the multiple stepper motors option.

| | Spindle Stepper Motor, and coordinate another axis | - Consider this option if you want to add a spherical or a curvilinear slide and have these controlled using a stepper motor. - This control system will control these and coordinate the movement with the spindle. - This system gives an amazing number of options; probably more than a person will master over many years. But that means it can be more difficult to learn to use. Go to question 3b
| | Other | If you want to design your own spindle drive system (e.g., a gear-driven motor), then do as you wish. Go to question 4.

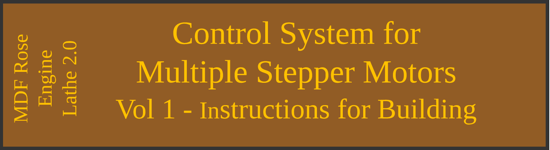
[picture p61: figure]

3b | Multiple Stepper Motor Controls: Do you want to build the system yourself? | Yes | Follow the directions outlined in the book to the right. You can get this document at https://mdfre2.colvintools.com/ We offer a kit of hard-to-obtain parts (https://colvintools.com/MDF-RE%202.0-ControlsKit-MultipleStepperMotors-HardToFindParts.html).
| | No | You will need to buy the Controls Kit - Multiple Stepper Motors (https://colvintools.com/MDF-RE%202.0-ControlsKit-MultipleStepperMotors.html).

4 | Do you have the need for a drilling frame (https://www.otbok.info/OT%20-%20LnT-Term-DrillingFrame.html)? | Yes | Generally, a cutting frame (https://www.otbok.info/OT%20-%20LnT-Term-CuttingFrame.html) is used, but you could use a drilling frame (https://www.otbok.info/OT%20-%20LnT-Term-DrillingFrame.html). If you are just getting started, I recommend you use a cutting frame.
| | No | If you don’t need a drilling frame (https://www.otbok.info/OT%20-%20LnT-Term-DrillingFrame.html) now, then I recommend you start with a cutting frame. You can add a drilling frame later.

5 | Do you expect to have multiple cutting and/or drilling frames? | Yes | Consider an Overhead Drive (https://www.otbok.info/OT%20-%20LnT-Term-OverheadDrive.html), approach. Jump to question 5a.
| | No | Take a look at the universal cutting frame (https://www.mandalaroseworks.com/product/cutting_frames) offered by Mandala Rose Works (https://www.mandalaroseworks.com/) (they also offer a drilling frame complete with collets). These have an integrated motor and are lower cost for a single item. There is a cost advantage for an Overhead Drive (https://www.otbok.info/OT%20-%20LnT-Term-OverheadDrive.html) when using it with multiple cutting frames or drilling frames. And there are other advantages to using one. These are outlined in the link above to the Ornamental Turning Book of Knowledge (http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

5a | Do you want to build your own overhead drive? | Yes | Jon Magill wrote an article on how to do this (http://www.rogueturner.com/root/Ornamental_Obsessions_files/Overhead-Spring2008.pdf) for the AAW (https://www.woodturner.org/).
| | No | You will need to buy the - Overhead Drive Kit (https://colvintools.com/MDF-RE%202.0-OverheadDriveKit.html) - Variable speed motor. You will need to order this item separately from Penn State Industries (https://www.pennstateind.com/store/TCLVSKIT2.html). The item needed is the Variable Speed Midi Lathe Conversion Kit, p/n TCLVSKIT2

5b | Do you want to make your own cutting (or drilling) frame? | Yes | Bill Ooms wrote a great set of instructions for building these. His web site is Ornamental Turning Chucks & Cutting Frames (https://www.billooms.com/resourceOT.html).
| | No | You will need to buy one. Consider one of these: - Universal Cutting Frame from Brad Davis - Universal Cutting Frame (https://lindowmachineworks.com/item/universal-cutting-frame-ucf/) from Lindow Machine Works

6 | Do you think this is a hobby you will be doing for a while? | Yes | You will need a cross slide (AKA, an X-Y table) and a tool holder. I recommend you go with the ones below from www.LittleMachineShop.com. - X-Y Table, p/n 2008 - Quick Change Tool Post, p/n 4701 - Tool Holder, p/n 2281 The X-Y table will need to be raised so that it can reach the spindle. For that follow the directions outlined in the book to the right. You can get this document at https://mdfre2.colvintools.com/.
| | Not sure | Consider using a drill press cross slide vice. It isn’t great but will get you up and running. And the cost is 1/3 of the other approaches.

## Spindle

May I get a spindle with spindle threads of 1 ¼”-8 (or M33)?

The kit as designed with a Morse Taper adapter which is we are offering either 1”-8 or 1 ¼”-8. There are good adapters available, and the user can certainly look into those.

May I get a spindle with a Morse taper?

This is being catered for in the design.

## Spindle Drive

Do you sell a kit with the hand crank as an option?

Haven spoken with a large number of MDF rose engine lathe users, all have motorized the spindle drive. Many have used geared motors with the speed controlled by changing the frequency of the power feed. Whilst that works, it is problematic at slower speeds as torque is lost. So the hand crank gets used when cutting at very slow speeds (e.g., when making the final passes on a cut).

Stepper motors provide a much better option as they maintain torque when running across the speed range used on the rose engine lathe. And, using stepper motors ensures a constant rotational speed at slower speeds, speeds measured in multiple minutes per revolution.

Do you sell a kit which accommodates multiple stepper motors?

There are two options at this time:

- A controls kit which implements a spindle stepper motor, or
- A controls kit which will control up to two stepper motors at the same time: The spindle stepper motor and one other. These are outlined in the user manual (which is available on-line in the MDF Rose Engine 2.0 Library (https://mdfre2.colvintools.com/) and kept up to date).

Can I get a different sized (or different amperage) stepper motor in my kit?

That is not an option we support at this time. The supplied kit is designed to work along known parameters. You are certainly welcome (and encouraged) to experiment.

Can I use a different sized (or different amperage) stepper motors?

The standards around which the system is developed are documented, and those are available on-line in the MDF Rose Engine 2.0 Library (https://mdfre2.colvintools.com/).

Can I get a different stepper motor controller or driver in my kit?

That is not an option we support at this time. The supplied kit is designed to work along known parameters. You are certainly welcome (and encouraged) to experiment.

Can I use a different stepper motor controller or driver?

The kit has been designed to easily utilize a very cost-effective approach to having a stepper motor drive the spindle. If you want to use a different controller or driver, you may, and are welcome to experiment.

To the extent that material may appear to be infringed, we assert that such alleged infringement is permissible under fair use principles in U.S. copyright laws. If you believe material has been used in an unauthorized manner, please contact me at ColvinTools@Gmail.com.

Portions of this document are copyrighted by Jon Magill and are used with his permission.

MDF Rose Engine Lathe 2.0 Frequently Asked Questions

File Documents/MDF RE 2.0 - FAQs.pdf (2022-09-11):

# MDF Rose Engine Lathe 2.0


# Frequently Asked Questions

## Version 1.2 08 January 2021

## MDF Rose Engine Lathe 2.0

## Frequently Asked Questions

This document is intended to answer frequently asked questions about the rose engine lathe kit sold on www.ColvinTools.com.

If you have any questions, please contact us at ColvinTools@Gmail.com.

Good luck.

Rich Colvin & Jack Zimmel

## MDF Rose Engine Lathe 2.0

## Frequently Asked Questions

Table of Contents

## MDF Rose Engine Lathe 2.0

## Frequently Asked Questions

4

The questions below are commonly asked, and responses are given to help the reader.

General

Does this design accommodate both rocking and pumping?
This kit provides for rocking, and there have been a number of people who have adding pumping capabilities. That capability is not provided by this kit at this time.
As we evolve and add to the system features over time, we will evaluate and consider adding it to the system. It will probably come as an add-on to the base system and will not require changes to the design we have delivered. None-the-less, if you are new to ornamental turning, there are so many capabilities provided by this machine that it will probably be a long time before you find the lack of pumping to be a limitation to your artistic endeavors (at least I haven’t yet).

Does this design accommodate a barrel approach with more than two rosettes?
The use of more than two rosettes at one time is something not accommodated by the design of this lathe. We have spoken with a large number of MDF rose engine lathe users, and none have expressed that having only two rosettes has limited their capabilities.
Instead, the ability to easily switch rosettes is a design feature for this machine. Other unique features for this machine include:
1. The ability to easily change the phasing of the rosettes (vs. the object) without having to perform any calculations.
2. The ability to change the alignment of one rosette against another.
So, if you are new to ornamental turning, this machine will enable you to pursue your artistic endeavors easily and without having to spend great amounts of time learning how.

## MDF Rose Engine Lathe 2.0

## Frequently Asked Questions

Where can I learn more about ornamental turning?
There are a number of great good options:
- Join the Ornamental Turners International. There is a forum on the web site which allows for questions to be posed and are typically answered relatively soon.
- Attend the Ornamental Turners International Symposium. There, you will meet many other users of the MDF rose engine lathe.
- Check out the Ornamental Turning Book of Knowledge. There is also a list of additional resources on that site.

What Do I Need to Get Started?
An MDF rose engine lathe consists of just a few parts, but we have broken up those parts to make it configurable for what you might want to do. The following questions are designed to help you get to the right answers for your situation.
0 Do you want to buy an off-the-shelf system with nothing required by you to get it up and running? | Yes | Used MDF rose engine lathes do become available from time to time, but not too often. Otherwise, you will need to build one as new MDF rose engine lathes are not sold as an off-the-shelf system. If this is a must for you, look at other options. There are some good ones, and they are listed at Buying a Rose Engine Lathe on the Ornamental Turning Book of Turning.
| No | Move on to question 1.

## MDF Rose Engine Lathe 2.0

## Frequently Asked Questions

### 1 Do you already

have one of the
original MDF
Rose Engine
Lathes?

(and are willing
to cannibalize it
for parts) | Yes

Many of the key parts can be moved to the newer design. This includes the
- Spindle and spindle bushings
- Rosette flange
- Pivot points
- Rubber & rubber parts
- Bungee & bungee parts
- Rosettes

If you added the stepper motor drive to your machine, those parts can be transferred over also. This includes
- Stepper motor mounting bracket with idler and bracket attachment hardware
- Spindle pulley
- Spindle stepper motor pulley
- Spindle drive timing belt
- Stepper motor
- Stepper motor controls
No | You will need the Base System Kit.

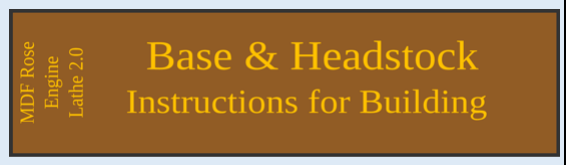
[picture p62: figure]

2 Do you want to cut the MDF parts yourself? | Yes | Follow the directions outlined in the book to the right. You can get this document at https://mdfre2.colvintools.com/.
| No | You will need to buy the pre-cut items in the Case Kit.

## MDF Rose Engine Lathe 2.0

## Frequently Asked Questions

### 3 How do you

want to drive
the spindle?

Spindle
Stepper
Motor

You will need to buy the Controls Kit - Spindle Stepper Motor. This kit provides all the parts
needed to attach the stepper motor to the
headstock, and to drive the spindle.

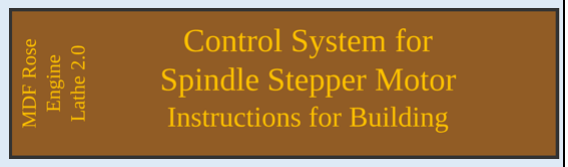
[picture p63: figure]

The other parts you need, and directions to assemble it are outlined in the book above. You can get this document at https://mdfre2.colvintools.com/

- This option is very easy to use.
- Stepper motors deliver consistent torque even at very slow speeds (minutes / revolution).
- It is much lower cost than the option for multiple stepper motors.
- If you take this option, most of the parts are reusable if you later decide to go with the multiple stepper motors option.
Spindle Stepper Motor, and coordinate another axis | • Consider this option if you want to add a spherical or a curvilinear slide and have these controlled using a stepper motor. • This control system will control these and coordinate the movement with the spindle. • This system gives an amazing number of options; probably more than a person will master over many years. But that means it can be more difficult to learn to use. Go to question 3b
Other | If you want to design your own spindle drive system (e.g., a gear-driven motor), then do as you wish. Go to question 4.

## MDF Rose Engine Lathe 2.0

## Frequently Asked Questions

3b Multiple Stepper Motor Controls: Do you want to build the system yourself? | Yes | Follow the directions outlined in the book to the right. You can get this document at https://mdfre2.colvintools.com/ We offer a kit of hard-to-obtain parts.

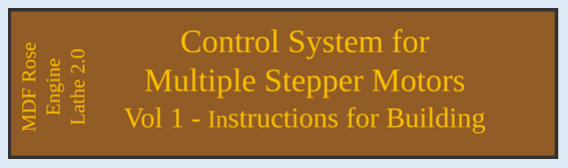
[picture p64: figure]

| No | You will need to buy the Controls Kit - Multiple Stepper Motors.
4 Do you have the need for a drilling frame? | Yes | Generally, a cutting frame is used, but you could use a drilling frame. If you are just getting started, I recommend you use a cutting frame.
| No | If you don’t need a drilling frame now, then I recommend you start with a cutting frame. You can add a drilling frame later.
5 Do you expect to have multiple cutting and/or drilling frames? | Yes | Consider an Overhead Drive, approach. Jump to question 5a.
| No | Take a look at the universal cutting frame offered by Mandala Rose Works (they also offer a drilling frame complete with collets). These have an integrated motor and are lower cost for a single item. There is a cost advantage for an Overhead Drive when using it with multiple cutting frames or drilling frames. And there are other advantages to using one. These are outlined in the link above to the Ornamental Turning Book of Knowledge.
5a Do you want to build your own overhead drive? | Yes | Jon Magill wrote an article on how to do this for the AAW.
| No | You will need to buy the • Overhead Drive Kit • Variable speed motor. You will need to order this item separately from Penn State Industries. The item needed is the Variable Speed Midi Lathe Conversion Kit, p/n TCLVSKIT2

## MDF Rose Engine Lathe 2.0

## Frequently Asked Questions

5b Do you want to make your own cutting (or drilling) frame? | Yes | Bill Ooms wrote a great set of instructions for building these. His web site is Ornamental Turning Chucks & Cutting Frames.
| No | You will need to buy one. Consider one of these: • Universal Cutting Frame from Brad Davis • Universal Cutting Frame from Lindow Machine Works
6 Do you think this is a hobby you will be doing for a while? | Yes | You will need a cross slide (AKA, an X-Y table) and a tool holder. I recommend you go with the ones below from www.LittleMachineShop.com. • X-Y Table, p/n 2008 • Quick Change Tool Post, p/n 4701 • Tool Holder, p/n 2281 The X-Y table will need to be raised so that it can reach the spindle. For that follow the directions outlined in the book to the right. You can get this document at https://mdfre2.colvintools.com/.

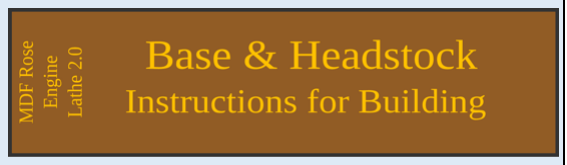
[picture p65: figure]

| Not sure | Consider using a drill press cross slide vice. It isn’t great but will get you up and running. And the cost is 1/3 of the other approaches.

## MDF Rose Engine Lathe 2.0

## Frequently Asked Questions

Spindle

May I get a spindle with spindle threads of 1 ¼”-8 (or M33)?
The kit as designed with a Morse Taper adapter which is we are offering either 1”-8 or 1 ¼”-8. There are good adapters available, and the user can certainly look into those.

May I get a spindle with a Morse taper?
This is being catered for in the design.

Spindle Drive

Do you sell a kit with the hand crank as an option?
Haven spoken with a large number of MDF rose engine lathe users, all have motorized the spindle drive. Many have used geared motors with the speed controlled by changing the frequency of the power feed. Whilst that works, it is problematic at slower speeds as torque is lost. So the hand crank gets used when cutting at very slow speeds (e.g., when making the final passes on a cut).
Stepper motors provide a much better option as they maintain torque when running across the speed range used on the rose engine lathe. And, using stepper motors ensures a constant rotational speed at slower speeds, speeds measured in multiple minutes per revolution.

Do you sell a kit which accommodates multiple stepper motors?
There are two options at this time:
- A controls kit which implements a spindle stepper motor, or
- A controls kit which will control up to two stepper motors at the same time: The spindle stepper motor and one other. These are outlined in the user manual (which is available on-line in the MDF Rose Engine 2.0 Library and kept up to date).

## MDF Rose Engine Lathe 2.0

## Frequently Asked Questions

Can I get a different sized (or different amperage) stepper motor in my kit?
That is not an option we support at this time. The supplied kit is designed to work along known parameters. You are certainly welcome (and encouraged) to experiment.

Can I use a different sized (or different amperage) stepper motors?
The standards around which the system is developed are documented, and those are available on-line in the MDF Rose Engine 2.0 Library.

Can I get a different stepper motor controller or driver in my kit?
That is not an option we support at this time. The supplied kit is designed to work along known parameters. You are certainly welcome (and encouraged) to experiment.

Can I use a different stepper motor controller or driver?
The kit has been designed to easily utilize a very cost-effective approach to having a stepper motor drive the spindle. If you want to use a different controller or driver, you may, and are welcome to experiment.

## MDF Rose Engine Lathe 2.0

## Frequently Asked Questions

To the extent that material may appear to be infringed, we assert that such alleged infringement is permissible under fair use principles in U.S. copyright laws. If you believe material has been used in an unauthorized manner, please contact me at ColvinTools@Gmail.com.

Portions of this document are copyrighted by Jon Magill and are used with his permission.

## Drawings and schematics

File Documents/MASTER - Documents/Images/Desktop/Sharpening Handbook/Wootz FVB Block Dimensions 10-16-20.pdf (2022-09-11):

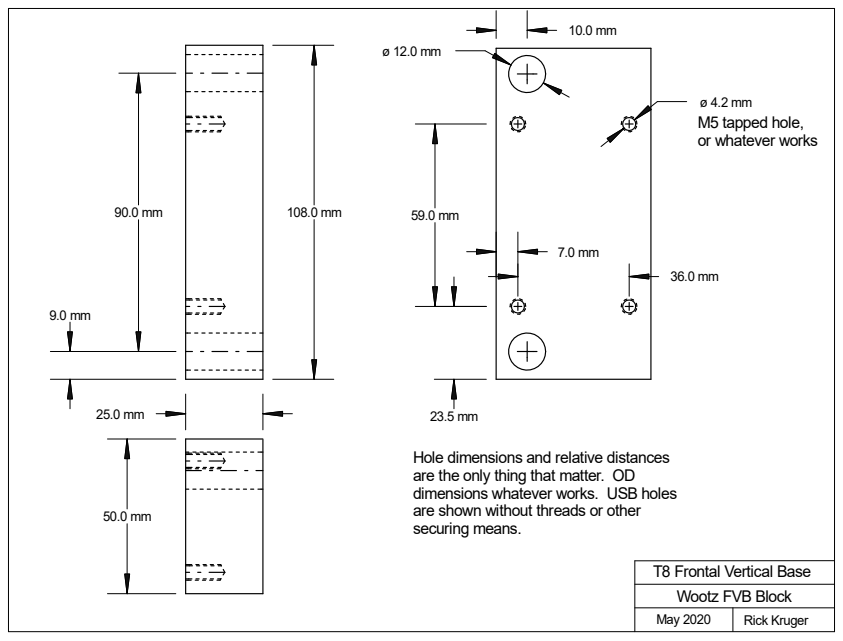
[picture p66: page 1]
Rick Kruger

M5 tapped hole,
or whatever works

Hole dimensions and relative distances
are the only thing that matter. OD
dimensions whatever works. USB holes
are shown without threads or other
securing means.

T8 Frontal Vertical Base
Wootz FVB Block
May 2020

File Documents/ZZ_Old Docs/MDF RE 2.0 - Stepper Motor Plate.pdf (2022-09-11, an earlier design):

# MDF Rose Engine Lathe 2.0

# with Stepper Motor Drive


# Stepper Motor Bracket & Associated Parts

## Version 1.0 03 August 2020

# MDF Rose Engine Lathe 2.0 Stepper Motor Bracket

You can purchase this from us at www.ColvinTools.com, or build them yourself. If you have any questions, please contact us at ColvinTools@Gmail.com.

Good luck and we hope you enjoy this machine as much as we.

Rich Colvin & Jack Zimmel

Permission is not granted to manufacture these for sale.

# Stepper Motor Bracket

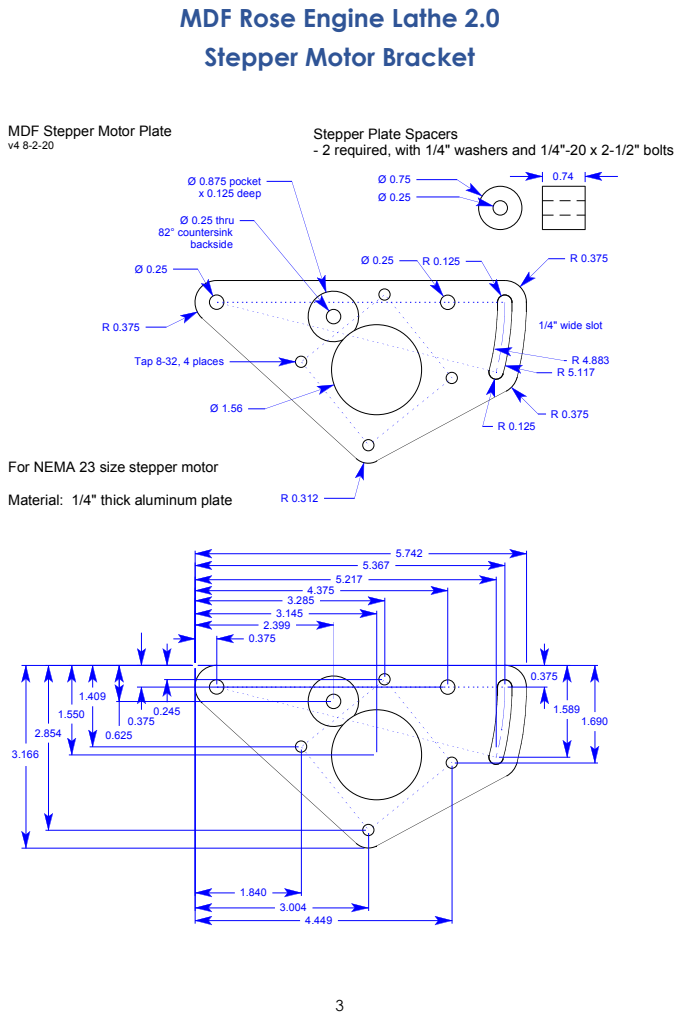
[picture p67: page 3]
Ø 0.25 thru; Ø 0.875 pocket; Tap 8-32, 4 places; 82° countersink backside; x 0.125 deep; 1/4" wide slot

MDF Stepper Motor Plate v4 8-2-20

Stepper Plate Spacers
- 2 required, with 1/4" washers and 1/4"-20 x 2-1/2" bolts

For NEMA 23 size stepper motor

Material: 1/4" thick aluminum plate

# Stepper Motor Bracket

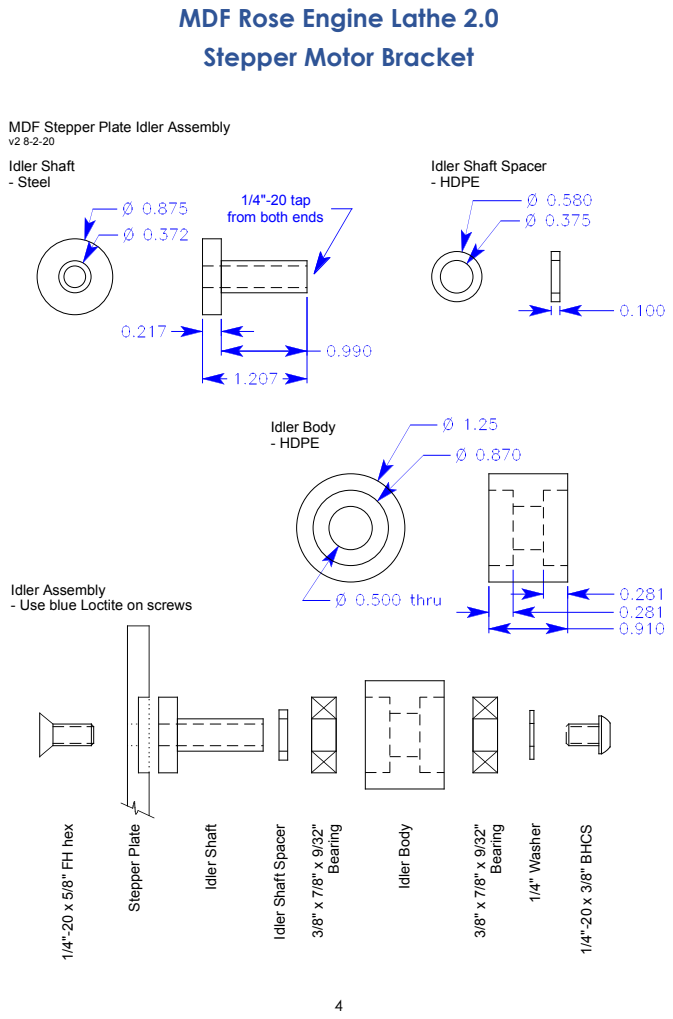
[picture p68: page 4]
Idler Shaft - Steel; Idler Body - HDPE; Ste; er Plate; Idler Shaft; Idler Shaft S; aring; Idler B; asher

MDF Stepper Plate Idler Assembly v2 8-2-20

Idler Shaft Spacer
- HDPE

1/4"-20 tap
from both ends

Idler Assembly
- Use blue Loctite on screws

# Stepper Motor Bracket

Parts for Stepper Drive Plate and Idler Assembly v1 - 8-2-20

Off-the-shelf Parts:

4 - #8-32 x 3/8" screws (Phillips or BHCS) for NEMA 23 motor 2 - 1/4"-20 x 2-1/2" Hex head bolts
3 - 1/4" washers, 2 for plate and 1 for idler
1 - 1/4"-20 x 5/8" FH hex drive screw
1 - 1/4"-20 x 3/8" BHCS

2 - 1/4"-20 dowel nuts for wood (.39" OD x .63" L) McM-C #90835A210 https://www.mcmaster.com/90835A210/

1 - 12T GT2 5mm pulley with .25" bore, 2 flanges, aluminum, for 9mm wide belt, SDP-SI #A 6A55-012DF0908 http://shop.sdp-si.com/catalog/product/?id=A%206a55-012df0908

2 - 3/8" x 7/8" x 9/32" shielded ball bearings MSC #01377498 https://www.mscdirect.com/product/details/01377498

1 - GT3 5mm pitch, 131T / 655mm long, 9mm wide Timing belt, Misumi #GBN655EV5GT-90 https://us.misumi-ec.com

Manufactured Parts:

1 - Stepper Plate - 1/4" thick plate, rough 5-3/4" x 3-1/4" 2 - Stepper plate spacers - 3/4" diameter aluminum rod
1 - Idler shaft - 7/8" diameter steel rod
1 - Idler shaft spacer - 5/8" diameter HDPE rod or similar 1 - Idler body - 1-1/4" diameter HDPE rod or similar

# Stepper Motor Bracket

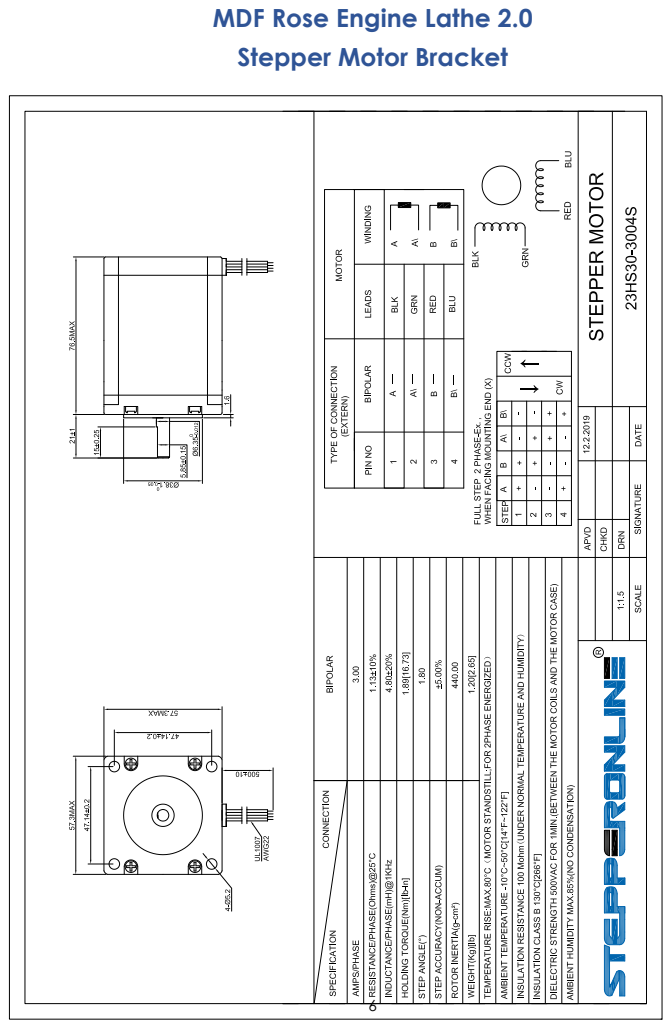
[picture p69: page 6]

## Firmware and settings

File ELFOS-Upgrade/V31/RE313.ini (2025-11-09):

; Rose Engine Ini file
; V3.1.3
;====================================
[Preferences]
;====================================
;
; Changed VendorId from 4 to 3.
;   - VendorId 3 = MDF Rose Engine Lathe 2.0
;   - VendorId 4 = Ed French's rose engine lathe, as modeled in Fusion 360
VendorId=4
;--------------------------------------------------------------
; THIS IS IGNORED FOR version 3.0.8
;
; Set MotorCount and CutterMotorPin based on this table
; 
;      PCB
;    Version   Teensy     MotorCount    CutterMotorPin
;    -------   ------     ----------    --------------
;      002c	   (any)	      4		    >16
;      002i	   (any)	      4		    >16
;      003	    3.2		      5		    n/a - can't be used
;      003	    3.5		      5		    >24
;      003	    3.6		      5		    >24
;
; Only set MotorCount to 5 if a 5th drive is connected to the board.
; This is needed for using M4.
MotorCount=5
;
; AuxillaryPin has replaced CutterMotorPin.
; CutterMotorPin must be greater than 16 on 4 motor board.
; CutterMotorPin must be greater than 24 on 5 motor board.
CutterMotorPin=26
AuxillaryPin=26
Auxillary Pin=26
;--------------------------------------------------------------
; Changed KeepSteppersEnabled from 0 to 1.  
; With DM542T drives, they need to be enabled
; for indexing, among other things.
; 0=Disabled, 1=Enabled
KeepSteppersEnabled=0
KeepSpindleEnabled=1
KeepXEnabled=0
KeepZEnabled=0
KeepM3Enabled=1
KeepM4Enabled=0
;--------------------------------------------------------------
; Spindle
Microsteps_Spindle=32
StepsPer360_Spindle=200
GearRatio_Spindle=9
;Polarity: Low=1, High=0
Polarity_Spindle=1
;--------------------------------------------------------------
;Z Axis
Microsteps_Z=32
StepsPer360_Z=200
DistancePer360_Z=0.31496
;Polarity: Low=1, High=0
Polarity_Z=1
; Hand: 0=Left, 1=Right
Leadscrew_Hand_Z=0
;--------------------------------------------------------------
;X Axis
XorAltXSelected=0
Microsteps_X=32
StepsPer360_X=200
DistancePer360_X=0.187
;Polarity: Low=1, High=0
Polarity_X=1
Leadscrew_Hand_X=0
;--------------------------------------------------------------
;Alternate X Axis
Microsteps_AltX=32
StepsPer360_AltX=200
DistancePer360_AltX=0.283
;Polarity: Low=1, High=0
Polarity_AltX=1
Leadscrew_Hand_AltX=1
;--------------------------------------------------------------
;M3 Axis
Microsteps_M3=32
StepsPer360_M3=200
GearRatio_M3=9
;Polarity: Low=1, High=0
Polarity_M3=1
; RadialOrLineal: 0=Radial, 1=Linear
RadialOrLineal_M3=0
;--------------------
; Linear Settings
DistancePer360_M3=1.02354
; Hand: 0=Left, 1=Right
Leadscrew_Hand_M3=1
;--------------------
; Radial Settings
M3Radius=5.124
;--------------------------------------------------------------
;M4 Axis
Microsteps_M4=32
StepsPer360_M4=200
GearRatio_M4=30
;Polarity: Low=1, High=0
Polarity_M4=1
; RadialOrLineal: 0=Radial, 1=Linear
RadialOrLineal_M4=1
;--------------------
; Linear Settings
DistancePer360_M4=0.0254
; Hand: 0=Left, 1=Right
Leadscrew_Hand_M4=1
;--------------------
; Radial Settings
M4Radius=11.258
;
;====================================
[Limits]
;====================================
; Set Limit Switches and Stop pins based on this table
; 
;     PCB 
;   Version   CutterMotorPin
;   -------   --------------
;     002c	   	 >16
;     002i	   	 >16
;     003	   	 >24
; 
; Note:  Limit switches are not useable with the Teensy 3.2
;
;Limit Switches and Stop pins must be greater than 16 on 4 motor board.
;Limit Switches and Stop pins must be greater than 24 on 5 motor board.
;
Min_Z=24
Max_Z=26
Min_X=24
Max_X=26
Min_M3=24
Max_M3=26
Min_M4=24
Max_M4=26
;--------------------------------------------------------------
;Stop spindle when limit hit = 0.  Leave spindle running =1
StopSpindle=0
; I had a problem setting this to 25 with the Teensy 3.2.
Stop=28
;Normally Closed=0, Normally Open=1
NC-NO=1
;
;====================================
[Returns]
;====================================
;
;Return
; All speeds and accellerations are in steps per second
MaxSpeed_Spindle=30000
Accel_Spindle=20000
MaxSpeed_Axis_Z=30000
Accel_Axis_Z=20000
MaxSpeed_Axis_X=30000
Accel_Axis_X=20000
MaxSpeed_Axis_M3=30000
Accel_Axis_M3=20000
MaxSpeed_Axis_M4=30000
Accel_Axis_M4=20000
;
;====================================
[Main]
;====================================
;
;Axis Ids:
;-----------------
;Z=1
;X=2
;M3=3
;M4=4
;Spindle=0
;-----------------
AxisId=1
;--------------------------------------------------------------
;Spindle
MaxSpeed_Spindle=15000
Accel_Spindle=15001
SpeedPercentage_Spindle=51
;--------------------------------------------------------------
;Z Axis
MaxSpeed_Z=4001
Accel_Z=5002
SpeedPercentage_Z=53
;--------------------------------------------------------------
;X Axis
MaxSpeed_X=4000
Accel_X=5005
SpeedPercentage_X=54
;--------------------------------------------------------------
;M3 Axis
MaxSpeed_M3 =5007
Accel_M3 =5008
SpeedPercentage_M3 =59
;--------------------------------------------------------------
;M4 Axis
MaxSpeed_M4 =5007
Accel_M4 =5008
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

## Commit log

2022-09-11 Initial Load
    [Curv-LimSwBase.stl, AA Rear Rubber.stl, AA-Align-Blk-v1.stl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]
2022-12-31 Activity Pin Documentation
2024-04-02 Quite a few Updates; changed to ELFOS
    [ELFOS-Face-Plate-Controls-v4.stl, ELFOS-Face-Plate-Power-v4.stl]
2024-09-08 Nextion 3D Print Files
    [Nextion 4.3e Base.stl, Nextion 4.3e Bezel.stl, Nextion 7i v1 Base - Angle.stl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]
2025-12-08 fixed 3D printing link
